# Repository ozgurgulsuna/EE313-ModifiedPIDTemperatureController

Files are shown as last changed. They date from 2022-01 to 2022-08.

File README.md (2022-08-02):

<h3 align="center" style=" border-bottom: none ;">EE313 Term Project </h3>
<p align="center">
   
<h2 align="center" style=" border-bottom: none ;">Design of an Autonomous Temperature Conditioning System Using Modified Analog PID Controller</h2>
<p align="center">

<h3 align="center" style=" border-bottom: none ;"> Project Summary </h3>
<p align="center">

<p align="justify">
&nbsp&nbsp Air conditioning can be described as the process of cooling, heating, moisturizing, dehumidifying, etc.
This method is utilized to create a more pleasant interior environment. In this project, you are required
to design an air conditioner system for small spaces. The system acquires heating, and cooling functions
and consists of one variable set input and four subsystems, namely, the control unit, display unit, sensing
unit, and the operation unit. The sensing unit provides the ambient temperature to the control unit, and
the temperature adjustment unit provides the desired temperature to the control unit. Figure 1 shows
the block diagram of the system.
</p>

<p align="center">
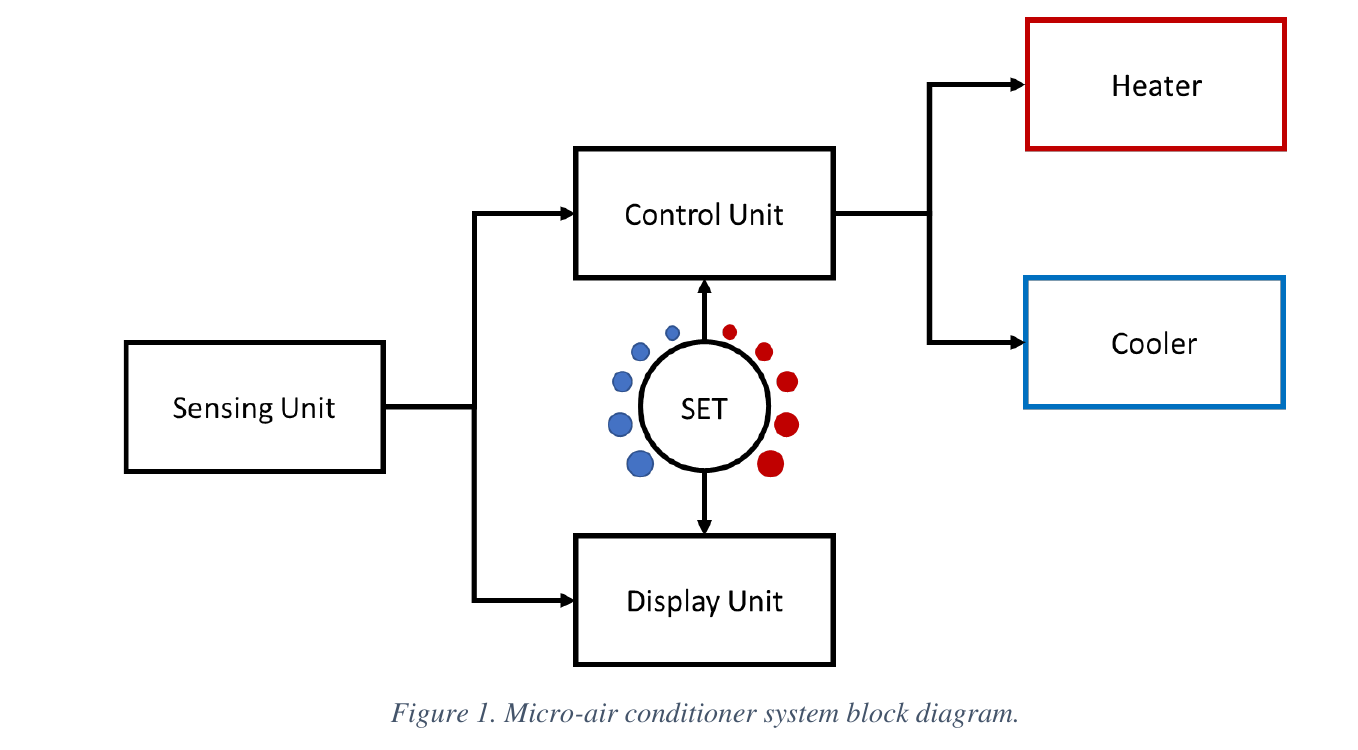
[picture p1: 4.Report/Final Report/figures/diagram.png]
 </a>
</p>

<p align="justify">
&nbsp&nbsp Thus to design a responsive, fast, and accurate temperature control system PID method is a feasible choice. One challenge, of applying PID method to this problem is that the heating and cooling processes are not symmetric. To compensate that, a modified PID control circuit will be introduced in this paper. Also, to avoid the EMI (Electromagnetic Interference) and noise problems, the circuit is designed on a PCB (Printed Circuit Board). The heating element is a nickel-chromium wire and the cooling element is an 12V DC fan. The fan and the heater are driven with a MOSFET switch which is controlled by the generated PWM (Pulse Width Modulation) signals. The PWM for each switch is generated by comparing a triangular wave with the PID outputs.
</p>
   
<p align="justify">
&nbsp&nbsp The ambient temperature is measured using the LM35 analog temperature sensor. The set temperature value is adjusted with a potentiometer. The set and ambient temperatures are displayed by the display unit which consist of RGB LEDs (Red Green Blue Light Emitting Diodes), a constant current LED drive utilized by a transconductance amplifier. The display unit designed in a way to emit red light at 24°Cand below, green light at 32°Cand blue light at 40°C and above. The display output for the temperature intervals between those values are produced by combining the colors in a way that a smooth transition is observed while the set and ambient temperatures are changed.
</p>

<p align="justify">
&nbsp&nbsp In this project, first the design methodology and the mathematical analysis of each unit will be discussed in detail in section II. The circuit schematics and their analysis will be given in this part. The mechanical design and the manufacturing will be discussed in section III. Then, thermal modelling of the system will be explained in section IV. The results of the performed LTspice simulations will be given in section V. The experimental results and the comparison with the simulation will follow in section VI. Finally, the conclusions will be drawn in section VII.
</p>

<h3 align="center" style=" border-bottom: none ;"> Report </h3>
<p align="center">
   
<p align="justify">
&nbsp&nbsp In this <a href="https://github.com/ozgurgulsuna/EE313-ModifiedPIDTemperatureController/blob/main/Design%20of%20an%20Autonomous%20Temperature%20Conditioning%20System%20Using%20Modifi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">report </a>, the design and implementation of an autonomous temperature conditioning system is demonstrated. Electrical and thermal systems are modelled in a single simulation environment with feedback loop closed. The PID method is shown that its applicable to this system, but due to the asymmetry of the reverse processes a modified PID circuit is proposed to damp oscillations of the system around the steady state, which is shown to be successful with the experimental results. Moreover, since the control signals are critical for the process, it is observed that filtering the noise with low and high pass filters and also avoiding the EMI effects with a careful PCB design procedure is essential for an accurate and reliable control mechanism.
</p>

<p align="center">
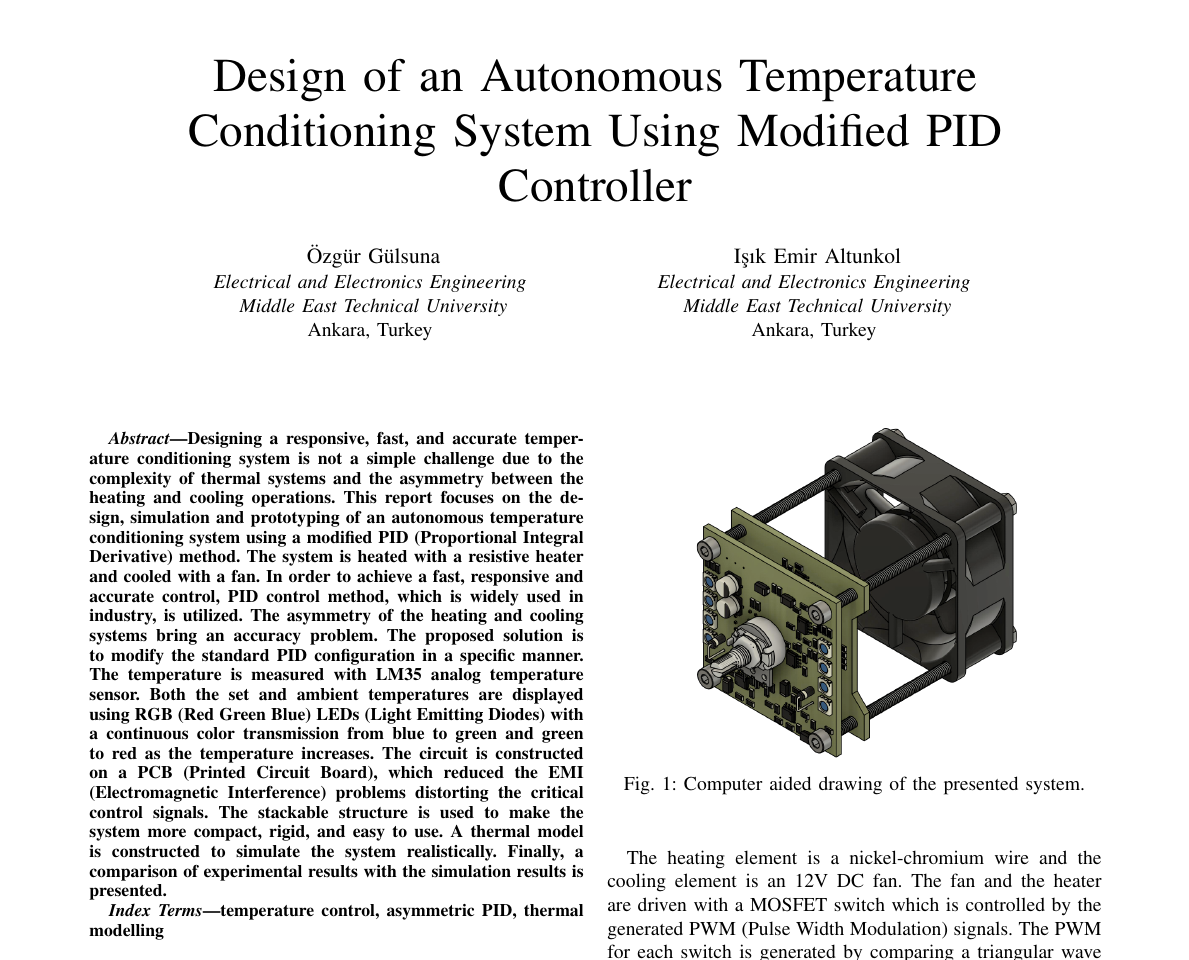
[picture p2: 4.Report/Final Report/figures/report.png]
   </a>
</p>

<h3 align="center" style=" border-bottom: none ;"> Photographs </h3>

<p align="center">
   
<p align="center">
    
    &nbsp&nbsp 
    
</p>

<p align="center">
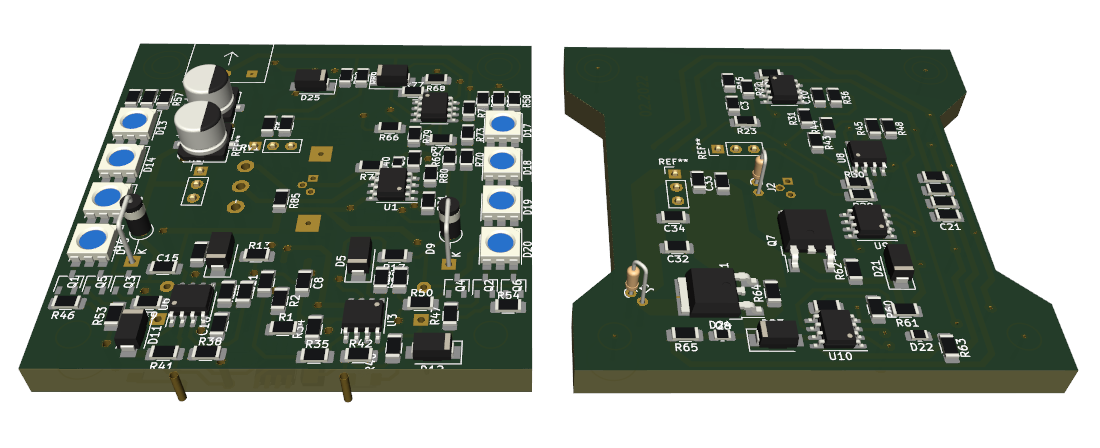
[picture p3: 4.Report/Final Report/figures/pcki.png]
    
</p>

<p align="center">
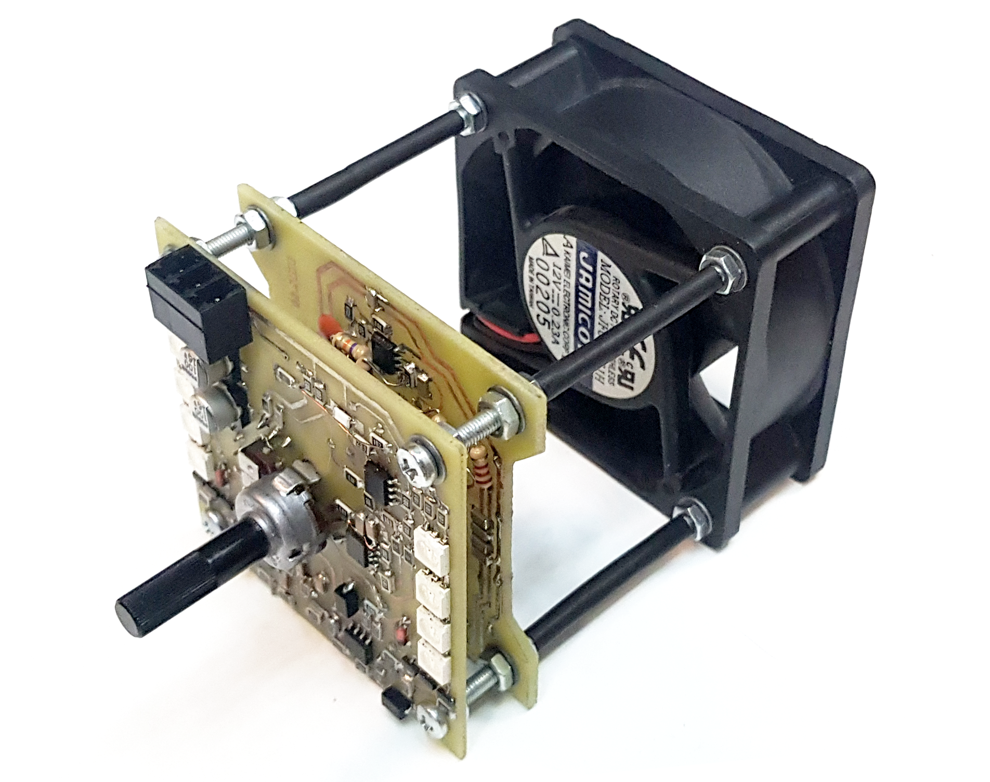
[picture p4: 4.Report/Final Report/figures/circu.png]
    
    &nbsp&nbsp 
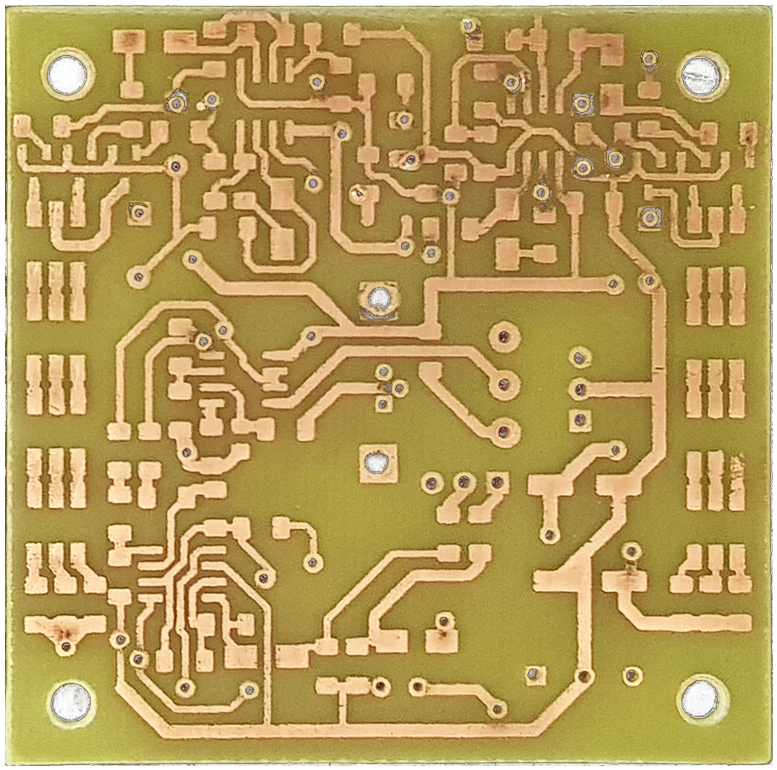
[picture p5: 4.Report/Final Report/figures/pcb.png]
    
</p>

<p align="center">
    
</p>
<p align="center">
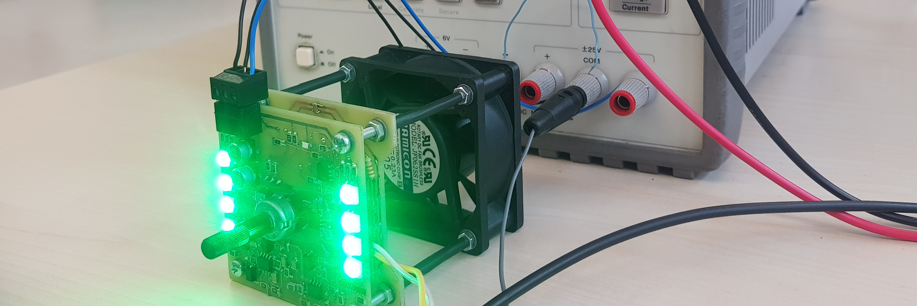
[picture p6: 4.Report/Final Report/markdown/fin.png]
    
</p>

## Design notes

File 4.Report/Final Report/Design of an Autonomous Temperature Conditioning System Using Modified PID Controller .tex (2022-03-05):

\documentclass[conference]{IEEEtran}
\IEEEoverridecommandlockouts
% The preceding line is only needed to identify funding in the first footnote. If that is unneeded, please comment it out.
\usepackage{cite}
\usepackage{amsmath,amssymb,amsfonts}
\usepackage{algorithmic}
\usepackage{graphicx}
\usepackage{textcomp}
\usepackage{xcolor}

\usepackage{physics}
\usepackage{amsmath}
\usepackage{tikz}
\usepackage{mathdots}
\usepackage{yhmath}
\usepackage{cancel}
\usepackage{color}
\usepackage{siunitx}
\usepackage{array}
\usepackage{multirow}
\usepackage{amssymb}
\usepackage{gensymb}
\usepackage{tabularx}
\usepackage{extarrows}
\usepackage{booktabs}
\usetikzlibrary{fadings}
\usetikzlibrary{patterns}
\usetikzlibrary{shadows.blur}
\usetikzlibrary{shapes}
\usepackage[figure]{ragged2e}

\usepackage{graphicx}
\usepackage{caption}
\usepackage{subcaption}

\def\BibTeX{{\rm B\kern-.05em{\sc i\kern-.025em b}\kern-.08em
    T\kern-.1667em\lower.7ex\hbox{E}\kern-.125emX}}
\begin{document}

\title{Design of an Autonomous Temperature Conditioning System Using Modified PID Controller\\
{}
}

\author{\IEEEauthorblockN{Özgür Gülsuna}
\IEEEauthorblockA{\textit{Electrical and Electronics Engineering} \\
\textit{Middle East Technical University}\\
Ankara, Turkey \\}
\and
\IEEEauthorblockN{Işık Emir Altunkol}
\IEEEauthorblockA{\textit{Electrical and Electronics Engineering} \\
\textit{Middle East Technical University}\\
Ankara, Turkey \\}
}

\maketitle

\begin{abstract}
Designing a responsive, fast, and accurate temperature conditioning system is not a simple challenge due to the complexity of thermal systems and the asymmetry between the heating and cooling operations. This report focuses on the design, simulation and prototyping of an autonomous temperature conditioning system using a modified PID (Proportional Integral Derivative) method. The system is heated with a resistive heater and cooled with a fan. In order to achieve a fast, responsive and accurate control, PID control method, which is widely used in industry, is utilized. The asymmetry of the heating and cooling systems bring an accuracy problem. The proposed solution is to modify the standard PID configuration in a specific manner. The temperature is measured with LM35 analog temperature sensor. Both the set and ambient temperatures are displayed using RGB (Red Green Blue) LEDs (Light Emitting Diodes) with a continuous color transmission from blue to green and green to red as the temperature increases. The circuit is constructed on a PCB (Printed Circuit Board), which reduced the EMI (Electromagnetic Interference) problems distorting the critical control signals. The stackable structure is used to make the system more compact, rigid, and easy to use. A thermal model is constructed to simulate the system realistically. Finally, a comparison of experimental results with the simulation results is presented.
\end{abstract}

\begin{IEEEkeywords}
temperature control, asymmetric PID, thermal modelling
\end{IEEEkeywords}

\section{Introduction}
In the industry, various control techniques are used for automating the physical processes. One of the simplest one is the on-off control, in which the operating unit is either actuated or not depending on other system and state parameters. However, the on-off control method is not flexible and accurate for most of the control problems. Because of that a slightly more advanced method called PID (Proportional Integral Derivative) is widely utilized in industry.

\begin{figure}[ht]
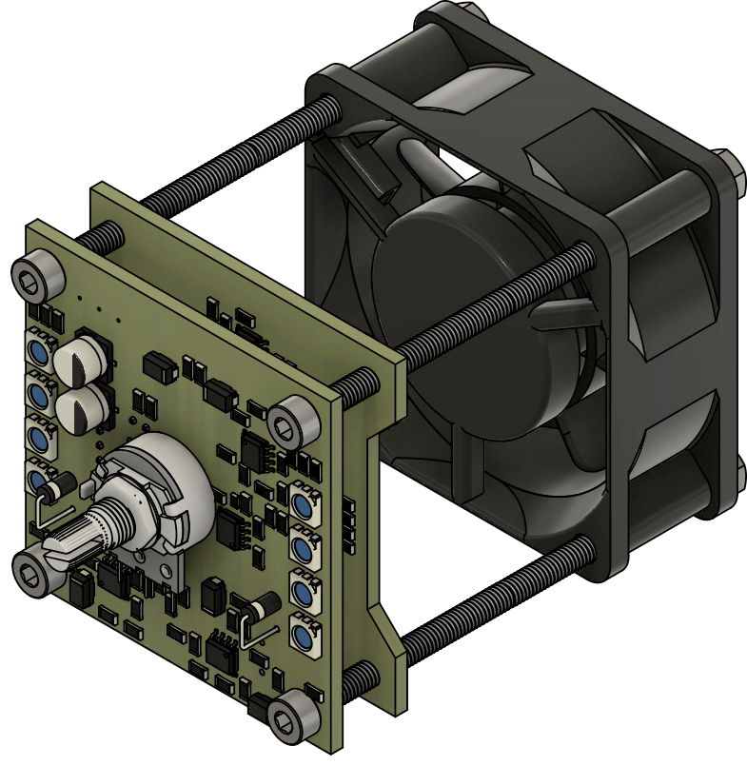
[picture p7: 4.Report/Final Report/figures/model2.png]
\centerline{}
\caption{Computer aided drawing of the presented system.}
\label{}
\end{figure}

Thus to design a responsive, fast, and accurate temperature control system PID method is a feasible choice. One challenge of applying PID method to this problem is that the heating and cooling processes are not symmetric. To compensate that, a modified PID control circuit will be introduced in this paper. Also, to avoid the EMI (Electromagnetic Interference) and noise problems, the circuit is designed on a PCB (Printed Circuit Board).

The heating element is a nickel-chromium wire and the cooling element is an 12V DC fan. The fan and the heater are driven with a MOSFET switch which is controlled by the generated PWM (Pulse Width Modulation) signals. The PWM for each switch is generated by comparing a triangular wave with the PID outputs.

The ambient temperature is measured using the LM35 analog temperature sensor. The set temperature value is adjusted with a potentiometer. The set and ambient temperatures are displayed by the display unit which consist of RGB LEDs (Red Green Blue Light Emitting Diodes), a constant current LED drive utilized by a transconductance amplifier. The display unit designed in a way to emit red light at 24\celsius and below, green light at 32\celsius and blue light at 40\celsius and above. The display output for the temperature intervals between those values are produced by combining the colors in a way that a smooth transition is observed while the set and ambient temperatures are changed.

In this paper, first the design methodology and the mathematical analysis of each unit will be discussed in detail in section II. The circuit schematics and their analysis will be given in this part. The mechanical design and the manufacturing will be discussed in section III. Then, thermal modelling of the system will be explained in section IV. The results of the performed LTspice simulations will be given in section V. The experimental results and the comparison with the simulation will follow in section VI. Finally, the conclusions will be drawn in section VII.

\section{Design Methodology and Mathematical Analysis}

In this section the design criteria are analyzed and solutions to each unit is presented with mathematical analysis of circuits are explained in detail.
 
\subsection{Sensing Unit}

The sensing unit consists of two independent sub-sections as mentioned above. The first element is the LM35 temperature sensor. This sensor gives a linear analog voltage output between -55$ ^\circ$C and 150  $ ^\circ$C in consequence it is applicable for the designs needs. The output of this sensor is amplified to ten folds such that 28$^\circ$C is scaled as 2.8 volts. This primary amplification facilitates the signal in order to better process it in the later stages. The second element is a potentiometer, which is basically a reference input and it is used in an adjustable resistor division configuration which scales the position to the range between 2 volts and 4.5 volts to cover the operation range of 20 to 45 $^\circ$C.

As in most of the sensory data acquisition, an initial low pass filter is used to clear out the unwanted high-frequency signals\cite{b1}. The design for this initial unit has an R-C low pass filter with the cut off frequency of 338.6 Hz \eqref{filter} which is selected as it is around 1/3 of the switching frequency of the operation unit. 
\begin{equation*}
f_{cut-off} =\frac{1}{2\pi RC} \rightarrow 338.6\ Hz \label{filter}
\end{equation*}

Another feature this section has is a linear regulator to supply the LM35 sensor. The selected voltage regulator is LM7805 which is a linear type and it is used to isolate the input of the temperature sensor from the unwanted swing of the input voltage.

\begin{figure}[h]
\centerline{}
\caption{Circuit schematic of the sensing unit}
\label{fig}
\end{figure}

The outputs of this unit are forwarded to the display and control units.

\subsection{Display Unit}

The display unit takes two inputs from the sensing unit: one is the amplified ambient temperature signal and the other is the set value, which is scaled to the same range with the temperature signal. This unit produces three different voltage signals to drive the RGB LEDs (one for each color), both for the set value display and the ambient temperature display. Since LED brightness is linearly proportional with its current, a transconductance amplifier with a BJT (Bipolar Junction Transistor) is used as a constant current LED driver (Fig.~\ref{transcondAmp}). Assuming the BJT is in forward active operation:

\begin{figure}[h]
\centerline{}
\caption{Transconductance amplifier as a constant current driver}
\label{transcondAmp}
\end{figure}

\begin{equation}
I_{C} = \beta \times \frac{V_{in}-V_{BE_{on}}}{R_{B}}\label{Iled}
\end{equation}

By \eqref{Iled}, it is observed that the input voltage signal is shifted downwards by $V_{BE_{on}}$ and then amplified by $\frac{\beta}{R_{B}}$. The collector current needed for the corresponding amplifier to obtain the required brightness for each color terminal is given in Fig.~\ref{ILED}.

\begin{figure}[h]
\centerline{}
\vspace{-1em}
\caption{Current vs temperature for each color terminal}
\label{ILED}
\end{figure}

To obtain the current signal in Fig.~\ref{ILED}, the voltage $V_{in}$ must be in the same shape, but shifted up by $V_{BE_{on}}$. This is why there is an amplifier stage which adds the diode drop value to the amplified set and temperature voltages. The schematic of these amplifiers is given in figure Fig.~\ref{dropSubtracter}. It can be easily observed that the input output relation for the amplifiers in figure Fig.~\ref{dropSubtracter} is given as:

\begin{equation}
V_{1}' = 2\cdot V_{1}+V_{BE_{on}}\label{drop_sub}
\end{equation}

\begin{figure}[h]
\centerline{}
\caption{Circuit schematic for $V_{BE_{on}}$ compensator}
\label{dropSubtracter}
\end{figure}

Note that the diode drop and the base emitter voltage drop of the transistors are approximately equal, since they are both made of silicon. The zener diode connected in shunt clips the voltage above 6.8V, which creates an upper limit for input voltage of the transconductance amplifier. Considering these, the process for obtaining the red and blue LED currents is the following: An offset is added to the temperature signal (or the set value signal, for the set display) to align its 0 value to the center of the operation region of the circuit (32\celsius). Then, this new signal is connected to $V_{1}$ \& $V_{2}$ terminals of the amplifier in figure Fig.~\ref{dropSubtracter}. Finally, determining $R_{C}=120k\Omega$ and connecting the output of the compensator to the input of the transconductance amplifier, we obtain the desired current signal.

A straightforward way to obtain the green LED current is to use an inverting summing amplifier and sum the voltage signals produced at the outputs of the figure Fig.~\ref{dropSubtracter}, and transmit this sum to the input of the transconductance amplifier. Note that the inverting sum result is a shifted version of the desired voltage, therefore the appropriate offset should be applied during the summing operation. Connecting all of the aforementioned parts, a display unit with a smooth and precise output is designed.

\subsection{Control Unit}
One of the more ingenious ways of controlling a dynamic system is PID method. This three-term controller is commonly used in the industry because of its accuracy and responsiveness \cite{b2}. Therefore it is selected as the main controller, more precisely a version with parallel configuration of action parameters of PID is selected. This approach isolates the parameters from each other which provides an easier tuning procedure for our system.

The system has two process variables in other words two outputs that can be controlled with our controller. These two actuators, heating element and fan, are working asynchronous with opposite reactions. This duality enforces an asymmetry in our system and it should be addressed to improve the response of the system \cite{b3}. The first solution comes in mind is to separate the controllers for each process variable but it increases the cost both in terms of components and tuning time. Our proposed method utilizes a single PID controller for the heater and its output is passed through a proportional term which then it is fed to the fan. This cascaded configuration presented in Fig.~\ref{parallelPID} enables the system to utilize its integral and derivative terms in both of the outputs. 

\begin{figure}[h]

\tikzset{every picture/.style={line width=0.75pt}} %set default line width to 0.75pt        

\begin{tikzpicture}[x=0.47pt,y=0.47pt,yscale=-1,xscale=1]
%uncomment if require: \path (0,235); %set diagram left start at 0, and has height of 235

%Shape: Resistor [id:dp04371691643945974] 
\draw   (135.96,39) -- (246.04,39) -- (246.04,79) -- (135.96,79) -- (135.96,39) -- cycle (105,59) -- (135.96,59) (246.04,59) -- (277,59) ;
%Shape: Resistor [id:dp10680848125616538] 
\draw   (135.96,94) -- (246.04,94) -- (246.04,134) -- (135.96,134) -- (135.96,94) -- cycle (105,114) -- (135.96,114) (246.04,114) -- (277,114) ;
%Shape: Resistor [id:dp6702844773190892] 
\draw   (135.96,150) -- (246.04,150) -- (246.04,190) -- (135.96,190) -- (135.96,150) -- cycle (105,170) -- (135.96,170) (246.04,170) -- (277,170) ;
%Straight Lines [id:da9493111687595024] 
\draw    (105,59) -- (105,170) ;
%Straight Lines [id:da22129182527616287] 
\draw    (105,59) -- (133.96,59) ;
\draw [shift={(135.96,59)}, rotate = 180] [color={rgb, 255:red, 0; green, 0; blue, 0 }  ][line width=0.75]    (10.93,-3.29) .. controls (6.95,-1.4) and (3.31,-0.3) .. (0,0) .. controls (3.31,0.3) and (6.95,1.4) .. (10.93,3.29)   ;
%Straight Lines [id:da46981664928370725] 
\draw    (105,114) -- (133.96,114) ;
\draw [shift={(135.96,114)}, rotate = 180] [color={rgb, 255:red, 0; green, 0; blue, 0 }  ][line width=0.75]    (10.93,-3.29) .. controls (6.95,-1.4) and (3.31,-0.3) .. (0,0) .. controls (3.31,0.3) and (6.95,1.4) .. (10.93,3.29)   ;
%Straight Lines [id:da05179885664599704] 
\draw    (105,170) -- (133.96,170) ;
\draw [shift={(135.96,170)}, rotate = 180] [color={rgb, 255:red, 0; green, 0; blue, 0 }  ][line width=0.75]    (10.93,-3.29) .. controls (6.95,-1.4) and (3.31,-0.3) .. (0,0) .. controls (3.31,0.3) and (6.95,1.4) .. (10.93,3.29)   ;
%Straight Lines [id:da6012096316257116] 
\draw    (246.04,114) -- (275,114) ;
\draw [shift={(277,114)}, rotate = 180] [color={rgb, 255:red, 0; green, 0; blue, 0 }  ][line width=0.75]    (10.93,-3.29) .. controls (6.95,-1.4) and (3.31,-0.3) .. (0,0) .. controls (3.31,0.3) and (6.95,1.4) .. (10.93,3.29)   ;
%Straight Lines [id:da20403881397537615] 
\draw    (288.5,170) -- (288.5,127.5) ;
\draw [shift={(288.5,125.5)}, rotate = 90] [color={rgb, 255:red, 0; green, 0; blue, 0 }  ][line width=0.75]    (10.93,-3.29) .. controls (6.95,-1.4) and (3.31,-0.3) .. (0,0) .. controls (3.31,0.3) and (6.95,1.4) .. (10.93,3.29)   ;
%Straight Lines [id:da27228914592677467] 
\draw    (288.5,59) -- (288.5,100.5) ;
\draw [shift={(288.5,102.5)}, rotate = 270] [color={rgb, 255:red, 0; green, 0; blue, 0 }  ][line width=0.75]    (10.93,-3.29) .. controls (6.95,-1.4) and (3.31,-0.3) .. (0,0) .. controls (3.31,0.3) and (6.95,1.4) .. (10.93,3.29)   ;
%Flowchart: Summing Junction [id:dp5290671545073427] 
\draw   (277,114) .. controls (277,107.65) and (282.15,102.5) .. (288.5,102.5) .. controls (294.85,102.5) and (300,107.65) .. (300,114) .. controls (300,120.35) and (294.85,125.5) .. (288.5,125.5) .. controls (282.15,125.5) and (277,120.35) .. (277,114) -- cycle ; \draw   (280.37,105.87) -- (296.63,122.13) ; \draw   (296.63,105.87) -- (280.37,122.13) ;
%Straight Lines [id:da746161281015258] 
\draw    (277,170) -- (288.5,170) ;
%Straight Lines [id:da11789860127120222] 
\draw    (277,59) -- (288.5,59) ;
%Straight Lines [id:da810785702729852] 
\draw    (78,114) -- (105,114) ;
%Straight Lines [id:da03181312676625048] 
\draw    (300,114) -- (510,114) ;
%Shape: Resistor [id:dp25780959233444034] 
\draw   (375.96,150) -- (486.04,150) -- (486.04,190) -- (375.96,190) -- (375.96,150) -- cycle (345,170) -- (375.96,170) (486.04,170) -- (517,170) ;
%Straight Lines [id:da21977667644036813] 
\draw    (345,170) -- (373.96,170) ;
\draw [shift={(375.96,170)}, rotate = 180] [color={rgb, 255:red, 0; green, 0; blue, 0 }  ][line width=0.75]    (10.93,-3.29) .. controls (6.95,-1.4) and (3.31,-0.3) .. (0,0) .. controls (3.31,0.3) and (6.95,1.4) .. (10.93,3.29)   ;
%Straight Lines [id:da016506681158132253] 
\draw    (345,170) -- (345,113.67) ;
%Straight Lines [id:da8718572314475974] 
\draw    (486.04,170) -- (515,170) ;
\draw [shift={(517,170)}, rotate = 180] [color={rgb, 255:red, 0; green, 0; blue, 0 }  ][line width=0.75]    (10.93,-3.29) .. controls (6.95,-1.4) and (3.31,-0.3) .. (0,0) .. controls (3.31,0.3) and (6.95,1.4) .. (10.93,3.29)   ;
%Straight Lines [id:da33938783257620053] 
\draw    (300,114) -- (515,114) ;
\draw [shift={(517,114)}, rotate = 180] [color={rgb, 255:red, 0; green, 0; blue, 0 }  ][line width=0.75]    (10.93,-3.29) .. controls (6.95,-1.4) and (3.31,-0.3) .. (0,0) .. controls (3.31,0.3) and (6.95,1.4) .. (10.93,3.29)   ;

% Text Node
\draw (177,49.4) node [anchor=north west][inner sep=0.75pt]  [font=\small]   {$K_{p} e( t)$};
% Text Node
\draw (168,103.4) node [anchor=north west][inner sep=0.75pt]  [font=\small]     {${\textstyle K_{i}\int e( t)}$};
% Text Node
\draw (173,159.4) node [anchor=north west][inner sep=0.75pt]   [font=\small]    {${\textstyle K_{d}\frac{d\ e( t)}{dt}}$};
% Text Node
\draw (68,91.4) node [anchor=north west][inner sep=0.75pt]   [font=\small]    {$e( t)$};
% Text Node
\draw (519.49,95.4) node [anchor=north west][inner sep=0.75pt]   [font=\small]    {$u_{heater}( t)$};
% Text Node
\draw (424.82,161.73) node [anchor=north west][inner sep=0.75pt]   [font=\small]    {$K_{p} e( t)$};
% Text Node
\draw (142,53.4) node [anchor=north west][inner sep=0.75pt]  [font=\large]  {${\displaystyle \mathbf{P}_{\mathbf{1}}}$};
% Text Node
\draw (142,103.4) node [anchor=north west][inner sep=0.75pt]  [font=\large]  {$\mathbf{I}$};
% Text Node
\draw (142,161.4) node [anchor=north west][inner sep=0.75pt]  [font=\large]  {$\mathbf{D}$};
% Text Node
\draw (382,161.4) node [anchor=north west][inner sep=0.75pt]  [font=\large]  {${\displaystyle \mathbf{P}_{\mathbf{2}}}$};
% Text Node
\draw (524.16,152.73) node [anchor=north west][inner sep=0.75pt]    {$u_{fan}( t)$};

\end{tikzpicture}

\caption{Proposed modified PID controller block diagram.}
\label{parallelPID}
\end{figure}

The controller in this section is implemented using operational amplifiers in an analogous way. First the error is generated using non inverting difference amplifier with unity gain. The error is then passed to three parallel stages which are proportional, integral and derivative terms. These configurations are inverting amplifiers by nature. Then the inverting summing amplifier is used to sum the action parameters into one. The circuit diagram of the control unit can be seen in Fig.~\ref{PIDcct}.

\begin{figure}[h]
    \centering
    
    \caption{PID implementation using operational amplifiers}
    \label{PIDcct}
\end{figure}

Key point of the control unit is the derivative term. Differentiator amplifier circuit acts as a high pass filter, in other words it enables high frequency components of the input signal to not only to pass but to be amplified \cite{b4}. It is an undesired condition since our switching frequency is around 1 kHz and it is easily coupled into the error signal. Amplifying this noise signal can cause the control signal to become erratic. Analyzing the differentiator circuit given in Fig.~\ref{diffe} shows this phenomena more clearly.

\begin{figure}[h]
    \centering
    
    \caption{Differentiator circuit to be analyzed.}
    \label{diffe}
\end{figure}

As seen in \eqref{derform} for high frequencies impedance of the capacitor is very small and in absence of $R_C$ resistor the gain is very high. In order to limit this gain a resistor of 1 k$\Omega$ is selected. 

\begin{equation}
V_{out} =\frac{-V_{error}R_D}{R_C + \frac{1}{sC_D}}\label{derform}
\end{equation}

\subsection{Operation Unit}

The purpose of the operation unit is to take the PID output signals from the control unit and produce PWM signals to drive the heater and the fan using a switch. The PWM method is utilized to convert the analog signals of the control unit into digital signals that can drive the MOSFETs. 

The first stage is a triangular wave generator (Fig.~\ref{triGen}). The left part in Fig.~\ref{triGen} is an astable multivibrator, which creates a square wave with the frequency given as:

\begin{equation}
f=\frac{1}{2R_{1}C_{1}\ln{(1+\frac{2R_{3}}{R_{2}})}}\label{freq}
\end{equation}

\begin{figure}[h]
\centerline{}
\caption{Circuit schematic of the triangular wave generator}
\label{triGen}
\end{figure}

Since it is aimed to achieve a PWM frequency around $1kHz$, the component values are chosen as $R_{1}=4.7k\Omega, C_{1}=22nF, R_{2}=1k\Omega, R_{3}=47k\Omega$ which brings $1.062kHz$ by \eqref{freq}. The multivibrator output is given to the integrator circuit, whose time constant is chosen as $R_{4}C_{2}=5ms$. Thus, $0.2$ time constant of the exponential waveform is produced, which is close enough to a triangular wave. After adding an offset and amplifying to an appropriate range, the triangular wave is supplied to two comparators to generate the PWM signals. The minimum points of the final triangular wave is higher than 0 volts by a couple hundred mVs, so that the heather or the fan does not act even for small disturbances in the control signals.

The PWM generating process for the heater is done in the conventional way. The triangular wave is compared with the PID heater output signal, and then a MOSFET is used as a switch to drive the heater with the PWM signal. The same process is applied to for the fan, except that after the cooperator, an additional compactor step is added to avoid powering the fan while the heater operates (Fig.~\ref{fanAND}). The second op-amp stage checks if the PID heater output is still higher than a certain threshold voltage (which is a positive value close to 0), and turns the switch on only if it is smaller than the threshold voltage. In this way, our design criteria is satisfied.

\begin{figure}[h]
\centerline{}
\caption{Circuit schematic of the comparators}
\label{fanAND}
\end{figure}

While the heater operates, the maximum power consumed by the system is less than 12W.

\section{Mechanical Design and Manufacturing}
Design of the mechanical system is formed around the biggest component which is the fan. It is 60x60 mm in width and 25 mm in depth with four bolt holes on four corners. These holes are used with 3mm bolts to construct a frame around the fan and circuit elements. These elements consist of operational amplifiers, LEDs, passive components such as resistors and capacitors and heater with the temperature sensor. All elements are fixed on printed circuit board (PCB) besides the fan. To satisfy the small form factor criteria PCB dimensions are selected again 60x60 mm and surface mount components are used. 

Heater element is a nickel-chromium wire which is used in electric heaters.The wire is wrapped into a spring shape and formed into a circle around the temperature sensor.This element has advantages such as enduring high temperatures, having a relatively high resistance which makes it smaller and being malleable. 

The power connector has three pins 12V, ground and -12V respectively. It connects only one way which makes it more convenient.

PCB is designed to form the circuit on. This technology has two advantages on analog circuits. The first one is with careful track planning noise susceptibility is reduced. The parasitic resistances, inductances and capacitances are also minimized. The second advantage is its rigidity and compactness. Design of the PCB is done on KiCad which is an open-source circuit board drawing program. The design consist two double-sided boards with connectors in-between. This stackable composition has advantages in both initial testing of the boards and in isolating the power paths from signal paths. The more outer board consist of sensing unit, display unit and control unit. All of these units consume very little power and they produce the control signals. The second board only has the operation unit. The most of the power is directed through this board. The PWM method creates changing currents and when we look at the equation of induced voltage in \eqref{indVolt}. It can be observed that time altering magnetic field generated from AC currents of the PWM signals, induces emf voltage on the magnetically coupled regions of the circuit. This way the noise is transmitted on signal paths. 

\begin{equation}
V_{ind} = L\frac{di}{dt} \label{indVolt}    
\end{equation}

Separating the boards reduces this interference and effectively isolates the signal paths. 

Input bus capacitors and decoupling capacitors near the operational amplifiers are working in a similar manner. These components filter out the noise from the input source and reduce the conducted EMI (Electromagnetic Interference) between sections.

\begin{figure}[!tbp]
  \begin{subfigure}[b]{0.319\textwidth}
    
    \caption{print out of the design.}
    \label{PCB}
  \end{subfigure}
  \hfill
  \begin{subfigure}[b]{0.158\textwidth}
    
    \caption{Printed circuit.}
    \label{}
  \end{subfigure}
  \begin{subfigure}{0.5\textwidth}
    
    \caption{3D model of the circuit board.}
  \end{subfigure}
  \caption{Digital and manufactured outputs of the PCB.}
\end{figure}

Manufacturing of this PCB is done with copper etching process using basic tools such as laser toner printer, clothes iron and corrosive chemicals. The printouts of the PCB for both boards and layers with processed PCB can be seen in Fig.\ref{PCB}.

\begin{figure}
\centerline{}
\caption{Hardware prototype of the designed temperature conditioning system.}
\end{figure}

\section{Thermal Modeling}
This project is composed of two mediums, electrical and thermal. The thermal system consist of heater, fan, temperature sensor and materials in-between. The electrical circuit is as mentioned, consist of the required circuitry to convert the electrical energy to thermal energy. 

In order to simulate the system as a whole it is needed to model the thermal system in electrical analogy. In this analogy, voltage corresponds to the temperature, current corresponds to the heat transfer ratio i.e. power and resistance  corresponds to the thermal resistance. Considering the elements of the thermal system the network is modeled as in Fig. \ref{Thermal}. $R_{\Theta HA}$ is the thermal resistance between the heater and ambient, $R_{\Theta HS}$ is between heater and sensor and $R_{\Theta SA}$ is between sensor and the ambient. The heater is a power controlled current source and the ambient is a fixed voltage source at the room temperature. Lastly the thermal capacitance of the temperature senor is given $C_{sens}$ and nickel-chromium wire is assumed to have very low thermal capacitance while it is very high for the ambient air.

From the datasheet of the LM35 temperature sensor we can find that $R_{\Theta SA}$ is 180 $^\circ C/W$ for the still air. To find the thermal resistance between the heater and the temperature sensor a test is conducted where a known power is applied to the heater and from the temperature difference between the ambient and the sensor with known $R_{\Theta SA}$ the heat flow ratio through the sensor to the ambient is calculated, that is:

\begin{equation}
    \frac{V_{sense}-V_{ambient}}{R_{\Theta SA}}=I_{branch1}
\end{equation}

\begin{equation}
    \frac{V_{heater}-V_{sens}}{I_{branch1}}=R_{\Theta HS}
\end{equation}

\begin{figure}[h]

\centering

\tikzset{every picture/.style={line width=0.75pt}} %set default line width to 0.75pt        

\begin{tikzpicture}[x=0.65pt,y=0.65pt,yscale=-1,xscale=1]
%uncomment if require: \path (0,241); %set diagram left start at 0, and has height of 241

%Shape: Resistor [id:dp19155962871671584] 
\draw   (263,120.55) -- (274.27,120.55) -- (276.77,113) -- (281.78,128.1) -- (286.79,113) -- (291.8,128.1) -- (296.8,113) -- (301.81,128.1) -- (306.82,113) -- (311.83,128.1) -- (314.33,120.55) -- (325.6,120.55) ;
%Shape: Capacitor [id:dp5418351324101072] 
\draw   (351.2,120.55) -- (351.2,152.61) (367.35,159.74) -- (335.05,159.74) (367.35,152.61) -- (335.05,152.61) (351.2,159.74) -- (351.2,191.8) ;
%Straight Lines [id:da2477799830980456] 
\draw    (325.6,120.55) -- (351.2,120.55) ;
%Straight Lines [id:da628273924807907] 
\draw    (351.2,120.55) -- (376.8,120.55) ;
%Shape: Resistor [id:dp5586121261918382] 
\draw   (376.8,120.55) -- (388.07,120.55) -- (390.57,113) -- (395.58,128.1) -- (400.59,113) -- (405.6,128.1) -- (410.6,113) -- (415.61,128.1) -- (420.62,113) -- (425.63,128.1) -- (428.13,120.55) -- (439.4,120.55) ;
%Straight Lines [id:da07949068449386076] 
\draw    (237.4,120.55) -- (263,120.55) ;
%Straight Lines [id:da6123881332149554] 
\draw    (439.4,120.55) -- (465,120.55) ;
%Flowchart: Connector [id:dp3224089439007152] 
\draw   (449.15,156.25) .. controls (449.15,147.5) and (456.25,140.4) .. (465,140.4) .. controls (473.75,140.4) and (480.85,147.5) .. (480.85,156.25) .. controls (480.85,165) and (473.75,172.1) .. (465,172.1) .. controls (456.25,172.1) and (449.15,165) .. (449.15,156.25) -- cycle ;
%Straight Lines [id:da8184153667034564] 
\draw    (465,120.55) -- (465,140.4) ;
%Straight Lines [id:da051595058920608006] 
\draw    (465,172.1) -- (465,191.95) ;
%Straight Lines [id:da6642435742487613] 
\draw    (237.4,120.55) -- (237.4,140.4) ;
%Straight Lines [id:da8967564739142377] 
\draw    (237.4,172.1) -- (237.4,191.95) ;
%Flowchart: Connector [id:dp07363181952530651] 
\draw   (221.55,156.25) .. controls (221.55,147.5) and (228.65,140.4) .. (237.4,140.4) .. controls (246.15,140.4) and (253.25,147.5) .. (253.25,156.25) .. controls (253.25,165) and (246.15,172.1) .. (237.4,172.1) .. controls (228.65,172.1) and (221.55,165) .. (221.55,156.25) -- cycle ;
%Shape: Ground [id:dp6306543326034124] 
\draw   (228.58,197.97) -- (237.4,210) -- (246.23,197.97) -- (228.58,197.97) -- cycle (237.4,191.95) -- (237.4,197.97) ;
%Shape: Ground [id:dp3092481158515603] 
\draw   (342.38,197.82) -- (351.2,209.85) -- (360.03,197.82) -- (342.38,197.82) -- cycle (351.2,191.8) -- (351.2,197.82) ;
%Shape: Ground [id:dp36715519214038794] 
\draw   (456.18,197.97) -- (465,210) -- (473.83,197.97) -- (456.18,197.97) -- cycle (465,191.95) -- (465,197.97) ;
%Straight Lines [id:da5206072269602895] 
\draw    (237.4,164) -- (237.4,148.4) ;
\draw [shift={(237.4,146.4)}, rotate = 90] [color={rgb, 255:red, 0; green, 0; blue, 0 }  ][line width=0.75]    (7.65,-2.3) .. controls (4.86,-0.97) and (2.31,-0.21) .. (0,0) .. controls (2.31,0.21) and (4.86,0.98) .. (7.65,2.3)   ;
%Shape: Resistor [id:dp2796434337397189] 
\draw   (319.2,77.35) -- (330.47,77.35) -- (332.97,69.8) -- (337.98,84.9) -- (342.99,69.8) -- (348,84.9) -- (353,69.8) -- (358.01,84.9) -- (363.02,69.8) -- (368.03,84.9) -- (370.53,77.35) -- (381.8,77.35) ;
%Straight Lines [id:da12366662536381101] 
\draw    (237.4,124.7) -- (237.4,77.35) ;
%Straight Lines [id:da01760570202550582] 
\draw    (237.4,77.35) -- (319.2,77.35) ;
%Straight Lines [id:da3751939511907125] 
\draw    (465,124.7) -- (465,77.35) ;
%Straight Lines [id:da29961110180248873] 
\draw    (381.8,77.35) -- (465,77.35) ;

% Text Node
\draw (451.2,144.4) node [anchor=north west][inner sep=0.75pt]  [font=\scriptsize]  {$ \begin{array}{l}
\mathbf{{\displaystyle +}}\\
\mathbf{{\displaystyle -}}
\end{array}$};
% Text Node
\draw (468.6,122.2) node [anchor=north west][inner sep=0.75pt]  [font=\small]  {$V_{amb}$};
% Text Node
\draw (389.8,92.4) node [anchor=north west][inner sep=0.75pt]  [font=\small]  {$R_{\theta SA}$};
% Text Node
\draw (275.8,93.2) node [anchor=north west][inner sep=0.75pt]  [font=\small]  {$R_{\theta HS}$};
% Text Node
\draw (332.2,49.4) node [anchor=north west][inner sep=0.75pt]  [font=\small]  {$R_{\theta HA}$};
% Text Node
\draw (199,121.4) node [anchor=north west][inner sep=0.75pt]  [font=\small]  {$P_{heat}$};
% Text Node
\draw (333.4,99.8) node [anchor=north west][inner sep=0.75pt]  [font=\small]  {$V_{sens}$};
% Text Node
\draw (356.6,129.6) node [anchor=north west][inner sep=0.75pt]  [font=\small]  {$C_{sens}$};

\end{tikzpicture}
\caption{Thermal network model using the electrical circuit elements}
\label{Thermal}
\end{figure}

Later the thermal resistance between the heater and the ambient can be found using again the same technique. Rest of the power flows through the branch 2, that is the upper branch.

\begin{equation}
    I_{power}-I_{branch1}=I_{branch2}
\end{equation}

\begin{equation}
    \frac{V_{heater}-V_{ambient}}{I_{branch2}}=R_{\Theta HA}
\end{equation}

A test voltage of 3.5V is applied to the heater and 0.56 ampere of current is passed resulting in 1.96 watts of power is dissipated on the resistor. From (6) thermal current on branch1 is 0.2033W and on branch2 it is 1.757W. At this stage nickel-chromium wire heated up to 131.5 $\celsius$. Steady state test shows that $R_{\Theta HS}$ is 650 $\celsius$/W, $R_{\Theta HA}$ is 62 $\celsius$/W.

Transient test is applied in order to measure the thermal capacitance. The time constant of the thermal circuit is measured with heating cycle of the system and $C_{sense}$ is measured to be 172 millifarads.

The last test applied in order to fully model the system is the cooling test.The fan effectively reduces the thermal resistance between the temperature sensor and the ambient temperature. For the test the fan is turned on and steady state values of the thermal resistances are measured with constant air flow over the system. Assuming the exiting air velocity is proportional with the motor speed in operation region andair velocity and the convection ratio of the system is in linear relation the thermal resistances are modeled as such\eqref{term}.

\begin{equation}
    R_{\Theta SA}=180-V_{fan}*12
    \label{term}
\end{equation}

\section{Simulation Results}

There are three critical specifications about this project that one can simulate. The first one is that the set and ambient display LEDs must cover the light spectrum with a smooth transition while the set and ambient temperatures cover the whole temperature range (24-40\celsius). The second one is that the fan and the resistor should never act at the same time. Finally, the control and the operation units work effective enough so that the temperature is adjusted rapidly and accurately. The simulations are done on LTspice, the data are exported and plotted in MATLAB. 

To show that the LED currents are as desired, a ramp input is given instead of the temperature measurement to the display unit, and the LED currents are observed in the simulation. Observed current signals are plotted in Fig.~\ref{displaySweep}, which is very close to the desired current signals in Fig.~\ref{ILED}

\begin{figure}
\centerline{}
\caption{Simulated LED currents vs time graphs for each color terminal}
\label{displaySweep}
\end{figure}

To show the other specifications are satisfied, it is needed to model the whole system in LTspice (including the thermal circuit in Fig.~\ref{Thermal}). Fig.~\ref{pwmSim} includes the PWM signals produced for the heater and the fan together. Since they do not intersect, it is concluded that the comparator works as desired.

\begin{figure}
\centerline{}
\caption{Simulated PWM signals for the heater and the fan}
\label{pwmSim}
\end{figure}

Using the same model, Fig.~\ref{pidSim} includes the set and the ambient temperature value waveforms. One can see from Fig.~\ref{pidSim} that the PID controller is able to reduce the error to a desired margin in a reasonable time for our model. Note that this simulation result is only a proof-of-concept showing that PID controller will work in the designed model. The tuning should be done experimentally.

\begin{figure}
\centerline{}
\caption{Simulated set and ambient temperature signals over time}
\label{pidSim}
\end{figure}

\section{Experimental Results}

In the first experiment, the base emitter voltages of the BJTs are measured using an oscilloscope. The results were consistent with the simulation results as expected. The transition was smooth and covering all the range.

In the second experiment, the set and the ambient temperature values are observed on the oscilloscope screen and the data is plotted in Fig.~\ref{pidRise} and Fig.~\ref{pidFall}. One can see that the full temperature can be adjusted and settled to a value very rapidly and accurately. The settling time is around 15 seconds, and the steady state error is strictly less than 1\celsius. As expected from the theoretical knowledge and simulation results, PID method works brilliantly in this specific case.

\begin{figure}
\centerline{}
\caption{Experimental set and ambient temperature signals (rise)}
\label{pidRise}
\end{figure}

\begin{figure}
\centerline{}
\caption{Experimental set and ambient temperature signals (fall)}
\label{pidFall}
\end{figure}

There are no detectable discrepancies with the theoretical and the simulation results, which means the accuracy of the models that are used are very high. Even if there are some deviations, they may be due to the non-idealities of the components and thermal disturbances.

\section{Conclusions}
In this paper, the design and implementation of an autonomous temperature conditioning system is demonstrated. Electrical and thermal systems are modelled in a single simulation environment with feedback loop closed. The PID method is shown that its applicable to this system, but due to the asymmetry of the reverse processes a modified PID circuit is proposed to damp oscillations of the system around the steady state, which is shown to be successful with the experimental results. Moreover, since the control signals are critical for the process, it is observed that filtering the noise with low and high pass filters and also avoiding the EMI effects with a careful PCB design procedure is essential for an accurate and reliable control mechanism.

\begin{thebibliography}{00}
\bibitem{b1} Y. Wu, J. P. Bobis and R. Gehman, "The design and analysis of an improved high air flow meter with analog/digital filters," [1992] Conference Record IEEE Instrumentation and Measurement Technology Conference, 1992, pp. 600-605, doi: 10.1109/IMTC.1992.245068.

\bibitem{b2}Kiam Heong Ang, G. Chong and Yun Li, "PID control system analysis, design, and technology," in IEEE Transactions on Control Systems Technology, vol. 13, no. 4, pp. 559-576, July 2005, doi: 10.1109/TCST.2005.847331.

\bibitem{b3}A. Baskys and V. Zlosnikas, "Asymmetric PID controller," IECON 2006 - 32nd Annual Conference on IEEE Industrial Electronics, 2006, pp. 219-223, doi: 10.1109/IECON.2006.347936.

\bibitem{b4} A. A. Kilov, V. N. Konstantyan, A. S. Sannikov, S. A. Sheptunov and A. A. Chetvertakov, "Applying Digital Filters to Suppress Noise in the Derivative Term of the PID Controller," 2021 International Conference on Quality Management, Transport and Information Security, Information Technologies (IT&QM&IS), 2021, pp. 301-304, doi: 10.1109/ITQMIS53292.2021.9642889.

\end{thebibliography}
\end{document}

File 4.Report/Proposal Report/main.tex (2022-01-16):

% Template last modified by Jake Hart; please contact course staff if you have any questions regarding using this template

\documentclass{METUHW} % You must have the cisXXX .cls file in your project or working directory (i.e. the same directory as this document) 
\HWno{1} % Enter the number of the homework you are working on
\HWcourse{EE313} % Enter the course department and number here
\HWpartner{Özgür Gülsuna} % If your class allows group work, put your partners here
\usepackage{amsmath}
\usepackage{calc}
\usepackage{xcolor}\pagecolor{white}
\usepackage[linguistics]{forest}
\usepackage{listings}[language=matlab]
\usepackage{listings}
\usepackage{color}
\usepackage{xcolor}
\usepackage[colorinlistoftodos]{todonotes}
\usepackage{float}
\usepackage{circuitikz}
\usepackage{ragged2e}
\usepackage{steinmetz}

%includes for tikz
\usepackage{physics}
\usepackage{amsmath}
\usepackage{tikz}
\usepackage{mathdots}
\usepackage{yhmath}
\usepackage{cancel}
\usepackage{color}
\usepackage{siunitx}
\usepackage{array}
\usepackage{multirow}
\usepackage{amssymb}
\usepackage{gensymb}
\usepackage{tabularx}
\usepackage{extarrows}
\usepackage{booktabs}
\usetikzlibrary{fadings}
\usetikzlibrary{patterns}
\usetikzlibrary{shadows.blur}
\usetikzlibrary{shapes}

\usepackage{physics}
\usepackage{amsmath}
\usepackage{tikz}
\usepackage{mathdots}
\usepackage{yhmath}
\usepackage{cancel}
\usepackage{color}
\usepackage{siunitx}
\usepackage{array}
\usepackage{multirow}
\usepackage{amssymb}
\usepackage{gensymb}
\usepackage{tabularx}
\usepackage{extarrows}
\usepackage{booktabs}
\usetikzlibrary{fadings}
\usetikzlibrary{patterns}
\usetikzlibrary{shadows.blur}
\usetikzlibrary{shapes}

\restylefloat{table}

\definecolor{codegreen}{rgb}{0,0.5,0.5}
\definecolor{codegray}{rgb}{0.5,0.5,0.5}
\definecolor{codepurple}{rgb}{0.6,0.1,0.1}
\definecolor{backcolour}{rgb}{0.95,0.95,0.95}

\lstdefinestyle{mystyle}{
    backgroundcolor=\color{backcolour},   
    commentstyle=\color{codegreen},
    keywordstyle=\color{magenta},
    numberstyle=\tiny\color{codegray},
    stringstyle=\color{codepurple},
    basicstyle=\ttfamily\footnotesize,
    breakatwhitespace=false,         
    breaklines=true,                 
    captionpos=b,                    
    keepspaces=true,                 
    numbers=false,                    
    numbersep=5pt,                  
    showspaces=false,                
    showstringspaces=false,
    showtabs=false,                  
    tabsize=2
}

\lstset{style=mystyle}

\newcommand*{\CenterVdots}{\makebox[\widthof{(0,0),}][c]{\vdots}}

\begin{document}

\title{{%   <-- starts a group
\vspace{-3cm}
\scriptsize
\normalsize
\textbf{EE313 ANALOG ELECTRONICS LABORATORY \\ \small TERM PROJECT}\\
\large\\
}%   <-- ends that group

\textbf{
PROPOSAL REPORT\\
}
\small
Design of a Micro-Air Conditioner\\
\medskip
\medskip
\medskip
\small

Özgür Gülsuna 2307668 \hfill 16.01.2022\\
\raggedright
Işık Emir Altunkol 2442408 \hfill Time Spent: 12 hours

}

\author{ }
\date{ }
\maketitle

\vspace{-4em}

\justifying

    To design an air conditioning system, we need to have a sensing unit, display unit, control unit, and an operation unit. In this document, we will explain our approach to implement those functioning units one by one. \\
\medskip

\textbf{ \normalsize Sensing Unit}\\
\fontsğze
    Sensing unit is a simple unit consisting of a temperature sensor and its amplifier. For the actual sensor we are going to use LM35. It will give a voltage output which has a linear relation with the temperature in the specified range. Some of the other features of this sensor are, 4-30 V operation range and 0.5°C accuracy. Amplifier at the output of the temperature sensor will enable us to isolate the different parts of the circuit which ensure its reliability and it will help us to scale the reading to a more useful range. We will place the sensor close enough to the heating and cooling elements so that we can change the temperature at the desired rate.\\

\medskip

\textbf{ \normalsize Display Unit}\\
    Display unit consists of two sets of RGB LEDs (red-green-blue light emitting diodes) in common anode configuration - one for displaying the set value, and the other for displaying the measured room temperature. We wanted to separate the LEDs to better visualize the operation of the system. As described in the project, we have a color bar indicating the temperatures. To achieve the same output we need to create three different signals for each LED.  Required signal for each color is shown in Figure 1. Series of operational amplifier structures will be used to generate the aforementioned signal. When it comes to driving the LEDs we will utilize bipolar junction transistors (BJTs). These semiconductor devices enable us to control the current of the individual LEDs which corresponds to their brightness. The selected topology is a common emitter amplifier. This structure is also named as  transconductance amplifier, which means that an input voltage produces an output current.

\begin{figure}[H]
\centering
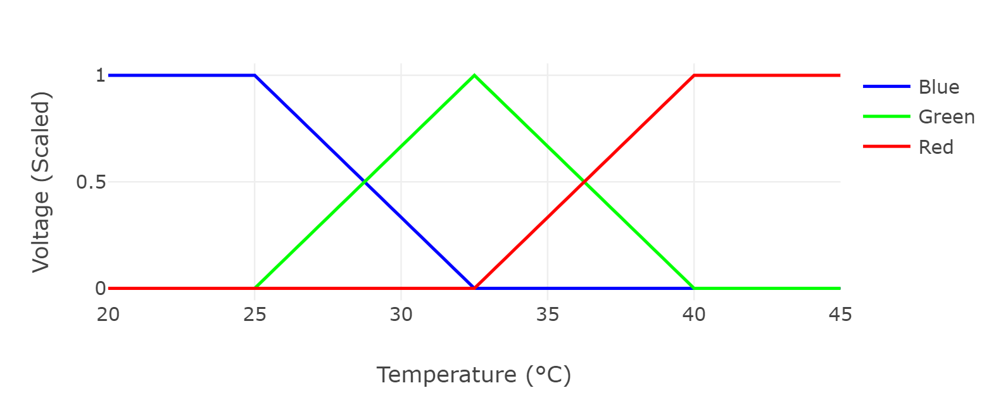
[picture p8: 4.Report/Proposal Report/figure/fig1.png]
\\
\centering
Figure 1. LED driving signals for each color.
\end{figure}

\textbf{ \normalsize Control Unit}\\
    Control unit has the highest complexity among others. It will have several parts for handling various tasks. First of all, it will take input from two different sources. First one will be the amplified output voltage of the temperature sensor. Second one will be the reading from the potentiometer. This unit will generate outputs for two different elements, heating and cooling respectively. We decided to implement a PID (proportional integral derivative) controller for this task, which is a controller with feedback. This way we can control the elements in an analogous fashion. We will take the input from the potentiometer as the set point and the amplified LM35 output as the process variable. The PID implementation will be done with operational amplifier configurations as shown in Figure 2. For op-amp selection, we will go with LM358 dual channel op-amps. They are cheap, reliable and suitable for the control unit. Also a dead-band is constructed at the end of this stage.

\centering

\tikzset{every picture/.style={line width=0.75pt}} %set default line width to 0.75pt        

\begin{tikzpicture}[x=0.75pt,y=0.75pt,yscale=-1,xscale=1]
%uncomment if require: \path (0,208); %set diagram left start at 0, and has height of 208

%Shape: Resistor [id:dp8858278922494136] 
\draw   (174.26,88.32) -- (190.4,88.32) -- (193.99,77.25) -- (201.16,99.39) -- (208.33,77.25) -- (215.5,99.39) -- (222.68,77.25) -- (229.85,99.39) -- (237.02,77.25) -- (244.19,99.39) -- (247.78,88.32) -- (263.92,88.32) ;
%Shape: Capacitor [id:dp03371552137820011] 
\draw   (168.33,41.69) -- (216.02,41.69) (226.61,20.5) -- (226.61,62.89) (216.02,20.5) -- (216.02,62.89) (226.61,41.69) -- (274.3,41.69) ;
%Shape: Triangle [id:dp98497243420744] 
\draw  [fill={rgb, 255:red, 217; green, 217; blue, 217 }  ,fill opacity=1 ] (394.24,102.94) -- (335.76,136.52) -- (335.76,69.35) -- cycle ;
%Straight Lines [id:da3971318773795933] 
\draw    (168.33,41.69) -- (168.33,88.32) ;
%Straight Lines [id:da3049997475460431] 
\draw    (274.3,41.69) -- (274.3,88.32) ;
%Straight Lines [id:da7159809408880349] 
\draw    (274.3,88.32) -- (335.34,88.32) ;
%Straight Lines [id:da9186521041305018] 
\draw    (174.26,88.32) -- (168.33,88.32) ;
%Straight Lines [id:da0908787872310326] 
\draw    (263.92,88.32) -- (274.3,88.32) ;
%Shape: Resistor [id:dp13518795960649532] 
\draw   (295.49,41.69) -- (311.63,41.69) -- (315.22,30.62) -- (322.39,52.77) -- (329.56,30.62) -- (336.73,52.77) -- (343.91,30.62) -- (351.08,52.77) -- (358.25,30.62) -- (365.42,52.77) -- (369.01,41.69) -- (385.15,41.69) ;
%Straight Lines [id:da3878971923579282] 
\draw    (295.49,41.69) -- (295.49,88.32) ;
%Shape: Capacitor [id:dp1987350161026391] 
\draw   (385.15,41.69) -- (432.83,41.69) (443.43,20.5) -- (443.43,62.89) (432.83,20.5) -- (432.83,62.89) (443.43,41.69) -- (491.12,41.69) ;
%Straight Lines [id:da7857458487620923] 
\draw    (394.24,102.94) -- (515.13,102.94) ;
%Straight Lines [id:da3195712557469328] 
\draw    (491.12,41.69) -- (491.12,102.94) ;
%Straight Lines [id:da9218474418090266] 
\draw    (295.49,115.87) -- (295.49,162.5) ;
%Straight Lines [id:da3520350954534184] 
\draw    (295.49,115.87) -- (335.88,115.87) ;
%Straight Lines [id:da9046341306409746] 
\draw    (295.49,162.5) -- (148.77,162.5) ;
%Straight Lines [id:da6420173241490861] 
\draw    (515.13,162.5) -- (295.49,162.5) ;
%Straight Lines [id:da18257571009246387] 
\draw    (168.33,88.32) -- (148.77,88.32) ;
%Flowchart: Connector [id:dp0488086244709538] 
\draw   (142.84,88.32) .. controls (142.84,86.68) and (144.17,85.35) .. (145.8,85.35) .. controls (147.44,85.35) and (148.77,86.68) .. (148.77,88.32) .. controls (148.77,89.96) and (147.44,91.29) .. (145.8,91.29) .. controls (144.17,91.29) and (142.84,89.96) .. (142.84,88.32) -- cycle ;
%Flowchart: Connector [id:dp7782162243873112] 
\draw   (142.84,162.5) .. controls (142.84,160.86) and (144.17,159.53) .. (145.8,159.53) .. controls (147.44,159.53) and (148.77,160.86) .. (148.77,162.5) .. controls (148.77,164.14) and (147.44,165.47) .. (145.8,165.47) .. controls (144.17,165.47) and (142.84,164.14) .. (142.84,162.5) -- cycle ;
%Flowchart: Connector [id:dp7350444455171572] 
\draw   (515.13,162.5) .. controls (515.13,160.86) and (516.45,159.53) .. (518.09,159.53) .. controls (519.73,159.53) and (521.06,160.86) .. (521.06,162.5) .. controls (521.06,164.14) and (519.73,165.47) .. (518.09,165.47) .. controls (516.45,165.47) and (515.13,164.14) .. (515.13,162.5) -- cycle ;
%Flowchart: Connector [id:dp4930242403173162] 
\draw   (515.13,102.94) .. controls (515.13,101.3) and (516.45,99.97) .. (518.09,99.97) .. controls (519.73,99.97) and (521.06,101.3) .. (521.06,102.94) .. controls (521.06,104.58) and (519.73,105.9) .. (518.09,105.9) .. controls (516.45,105.9) and (515.13,104.58) .. (515.13,102.94) -- cycle ;

% Text Node
\draw (339.35,106.62) node [anchor=north west][inner sep=0.75pt]   [align=left] {+};
% Text Node
\draw (341.37,77.77) node [anchor=north west][inner sep=0.75pt]   [align=left] {{\large -}};
% Text Node
\draw (205.6,103.2) node [anchor=north west][inner sep=0.75pt]    {$R_{1}$};
% Text Node
\draw (326.8,7.4) node [anchor=north west][inner sep=0.75pt]    {$R_{2}$};
% Text Node
\draw (189.2,8) node [anchor=north west][inner sep=0.75pt]    {$C_{1}$};
% Text Node
\draw (408.8,6.2) node [anchor=north west][inner sep=0.75pt]    {$C_{2}$};
% Text Node
\draw (140.8,122.8) node [anchor=north west][inner sep=0.75pt]    {$V_{in}$};
% Text Node
\draw (496,120.8) node [anchor=north west][inner sep=0.75pt]    {$V_{out}$};

\end{tikzpicture}

\\

\centering
Figure 2. PID controller implemented with single operational amplifier.\\

\medskip

\raggedright

\justifying

\textbf{ \normalsize Operation Unit}\\
    Operation unit is sort of a driver unit. In this section, output of the control unit is picked up and converted into pulse width modulation (PWM) signals so that our elements can be controlled more accurately. An oscillator will be implemented in this section to generate the PWM clock for the elements. This single clock will be utilized by both of the comparator blocks, which means that their frequency will be the same. Basically the triangle oscillator is compared with control signals to generate desired PWM signals for each output. Later these signals are fed onto mosfet bridges to adjust the power given to each element. The heating element is selected as a piece of nickel-chromium wire. The heating wire will be wrapped around our temperature sensor without touching to ensure more of the power is transferred onto the sensor. The resistance value for the wire will be chosen such that at most it will dissipate 10 watts of power. For cooling we will use a 12 V computer fan, which takes direct current voltage for an input. The power consumption of the selected fan is around 2 watts. Preliminary experiments showed that these power ratings will be fairly enough.\\
    
\medskip

\textbf{ \normalsize Mechanical Design}\\
Mechanical construction of the system is decided to be built upon the fan. The mounting holes of the fan will be used to carry the circuit and the sensor will be placed on the circuit and directed towards the fan and it will be surrounded by the heating wire. For this design our circuit will be carried over the printed circuit board (PCB) with surface mount components. KiCad is selected for the PCB drawing program since it is open source and easy to use . This approach not only shrinks the size of the circuit but also helps us to reduce the electromagnetic interference. In the end we hope this rigid construction will be aesthetically pleasing (see Figure 3).\\

\begin{figure}[H]
\centering

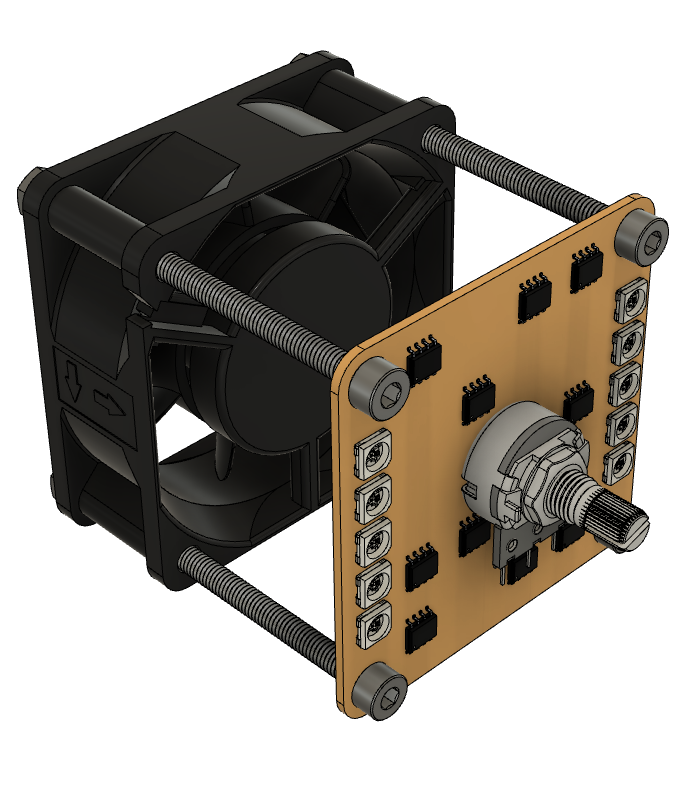
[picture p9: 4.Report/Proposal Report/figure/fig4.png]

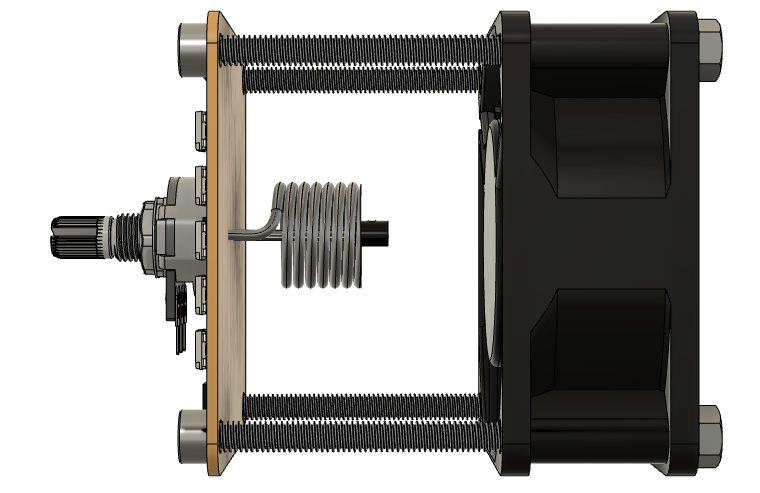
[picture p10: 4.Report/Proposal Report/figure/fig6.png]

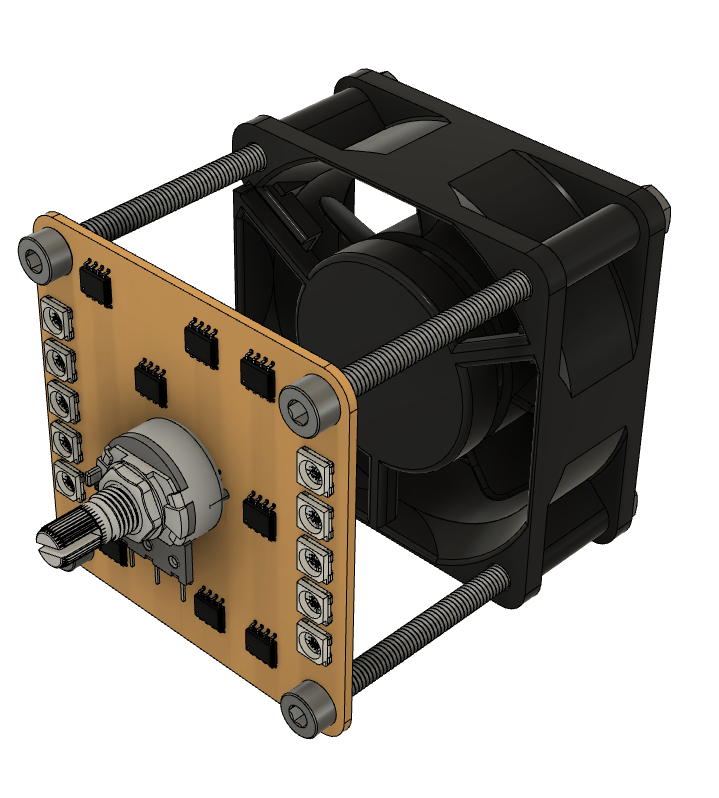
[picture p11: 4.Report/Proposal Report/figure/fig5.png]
\\
\centering
Figure 3. Computer aided drawing of the planned construct.
\end{figure}

\\

	As we work on this project, we will first precisely choose the components we use (with their values) and simulate our designs in LTspice by simulating each unit separately and simulating some of them together (if applicable). If we get the results we expected, we will move on to the prototyping stage where we build each unit on a breadboard and test them. After all these stages, the circuit is reconstructed on a PCB and mounted on the fan.
	
\vspace{-2em}

 \end{document}

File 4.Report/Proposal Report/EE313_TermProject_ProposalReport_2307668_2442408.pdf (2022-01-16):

EE313 ANALOG ELECTRONICS LABORATORY TERM PROJECT

# PROPOSAL REPORT

Design of a Micro-Air Conditioner

Ozg¨ur G¨ulsuna 2307668 ¨ | 16.01.2022
I¸sık Emir Altunkol 2442408 | Time Spent: 12 hours

To design an air conditioning system, we need to have a sensing unit, display unit, control unit, and an operation unit. In this document, we will explain our approach to implement those functioning units one by one.

Sensing Unit
Sensing unit is a simple unit consisting of a temperature sensor and its amplifier. For the actual sensor we are going to use LM35. It will give a voltage output which has a linear relation with the temperature in the specified range. Some of the other features of this sensor are, 4-30 V operation range and 0.5°C accuracy. Amplifier at the output of the temperature sensor will enable us to isolate the different parts of the circuit which ensure its reliability and it will help us to scale the reading to a more useful range. We will place the sensor close enough to the heating and cooling elements so that we can change the temperature at the desired rate.

Display Unit
Display unit consists of two sets of RGB LEDs (red-green-blue light emitting diodes) in common anode configuration - one for displaying the set value, and the other for displaying the measured room temperature. We wanted to separate the LEDs to better visualize the operation of the system. As described in the project, we have a color bar indicating the temperatures. To achieve the same output we need to create three different signals for each LED. Required signal for each color is shown in Figure 1. Series of operational amplifier structures will be used to generate the aforementioned signal. When it comes to driving the LEDs we will utilize bipolar junction transistors (BJTs). These semiconductor devices enable us to control the current of the individual LEDs which corresponds to their brightness. The selected topology is a common emitter amplifier. This structure is also named as transconductance amplifier, which means that an input voltage produces an output current.


Figure 1. LED driving signals for each color.

Control Unit
Control unit has the highest complexity among others. It will have several parts for handling various tasks. First of all, it will take input from two different sources. First one will be the amplified output voltage of the temperature sensor. Second one will be the reading from the potentiometer. This unit will generate outputs for two different elements, heating and cooling respectively. We decided to implement a PID (proportional integral derivative) controller for this task, which is a controller with feedback. This way we can control the elements in an analogous fashion. We will take the input from the potentiometer as the set point and the amplified LM35 output as the process variable. The PID implementation will be done with operational amplifier configurations as shown in Figure 2. For op-amp selection, we will go with LM358 dual channel op-amps. They are cheap, reliable and suitable for the control unit. Also a dead-band is constructed at the end of this stage.

1

Proposal Report | EE313 | Fall 2021-2022

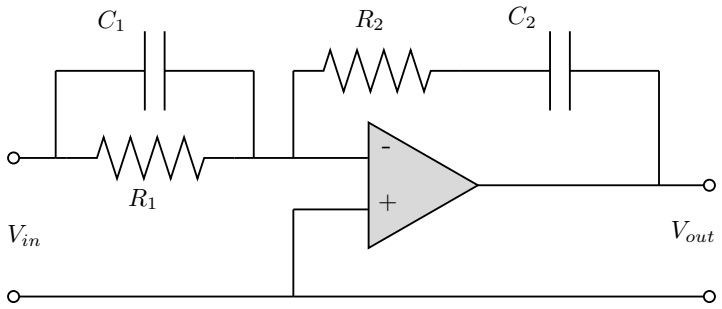
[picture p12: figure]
Vin; Vout

Figure 2. PID controller implemented with single operational amplifier.

Operation Unit
Operation unit is sort of a driver unit. In this section, output of the control unit is picked up and converted into pulse width modulation (PWM) signals so that our elements can be controlled more accurately. An oscillator will be implemented in this section to generate the PWM clock for the elements. This single clock will be utilized by both of the comparator blocks, which means that their frequency will be the same. Basically the triangle oscillator is compared with control signals to generate desired PWM signals for each output. Later these signals are fed onto mosfet bridges to adjust the power given to each element. The heating element is selected as a piece of nickel-chromium wire. The heating wire will be wrapped around our temperature sensor without touching to ensure more of the power is transferred onto the sensor. The resistance value for the wire will be chosen such that at most it will dissipate 10 watts of power. For cooling we will use a 12 V computer fan, which takes direct current voltage for an input. The power consumption of the selected fan is around 2 watts. Preliminary experiments showed that these power ratings will be fairly enough.

Mechanical Design
Mechanical construction of the system is decided to be built upon the fan. The mounting holes of the fan will be used to carry the circuit and the sensor will be placed on the circuit and directed towards the fan and it will be surrounded by the heating wire. For this design our circuit will be carried over the printed circuit board (PCB) with surface mount components. KiCad is selected for the PCB drawing program since it is open source and easy to use . This approach not only shrinks the size of the circuit but also helps us to reduce the electromagnetic interference. In the end we hope this rigid construction will be aesthetically pleasing (see Figure 3).

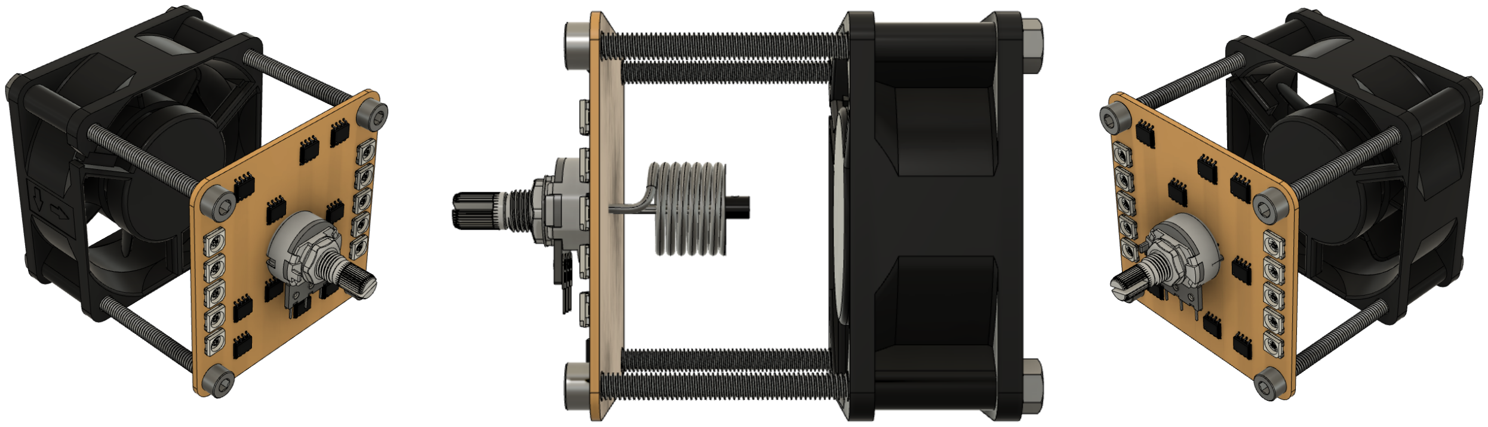
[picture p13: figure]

Figure 3. Computer aided drawing of the planned construct.

As we work on this project, we will first precisely choose the components we use (with their values) and simulate our designs in LTspice by simulating each unit separately and simulating some of them together (if applicable). If we get the results we expected, we will move on to the prototyping stage where we build each unit on a breadboard and test them. After all these stages, the circuit is reconstructed on a PCB and mounted on the fan.

2

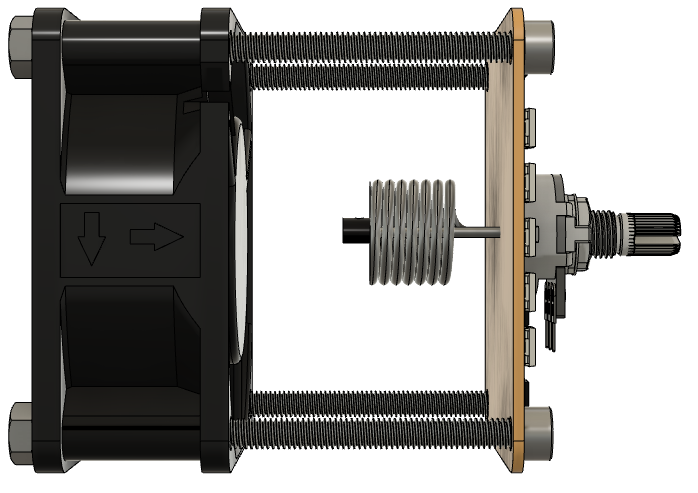
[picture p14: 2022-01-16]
4.Report/Proposal Report/figure/fig3.png

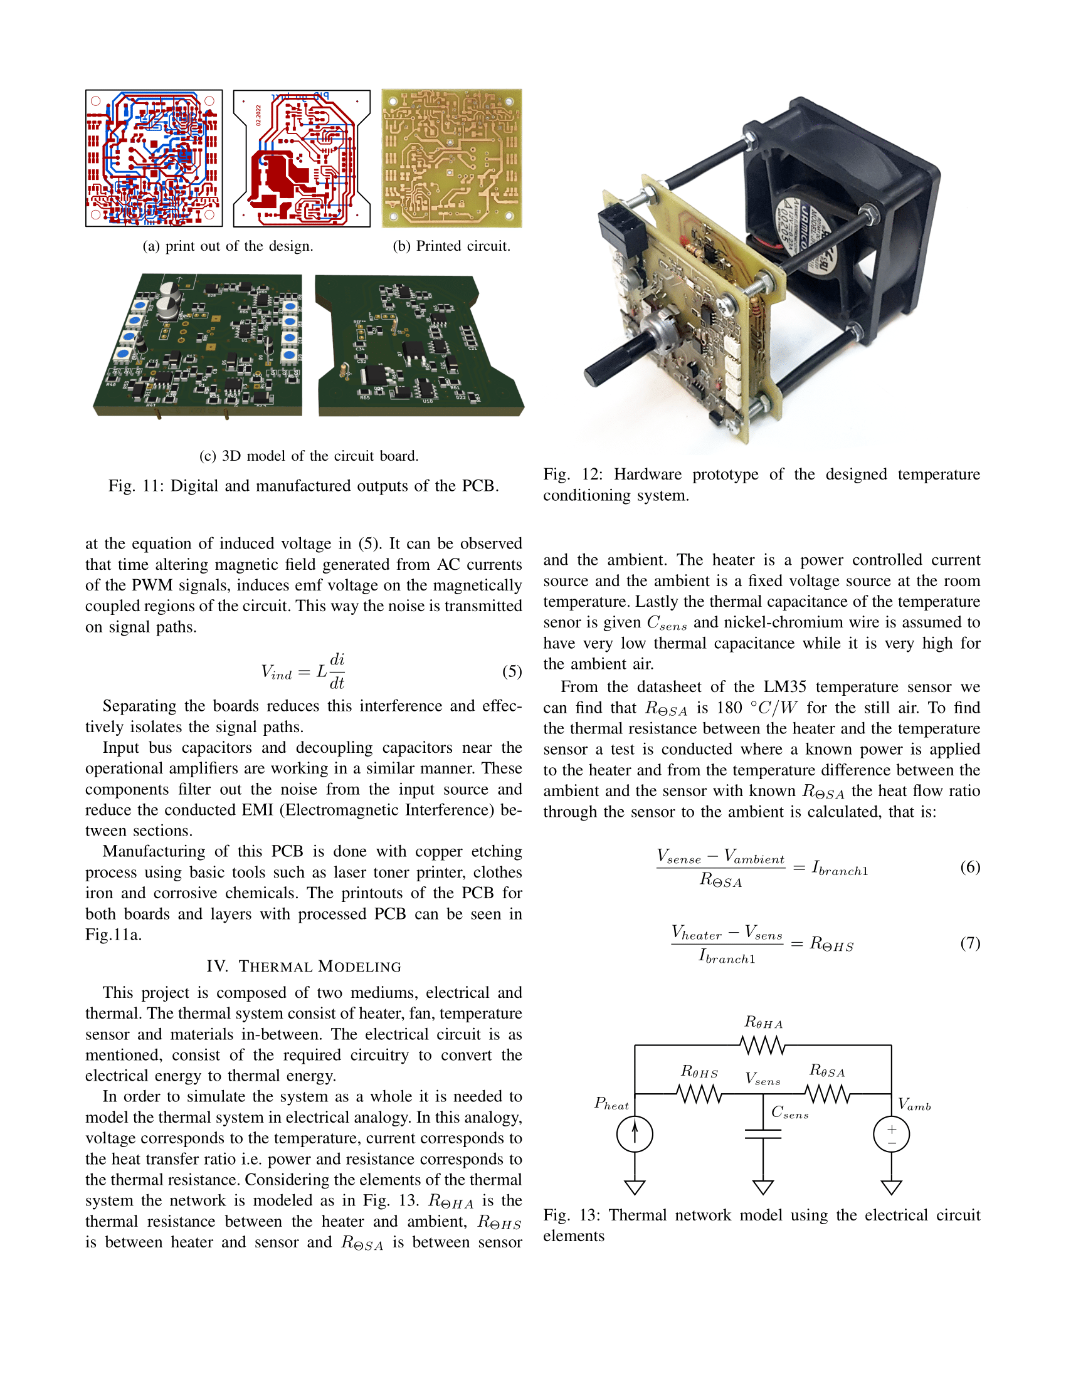
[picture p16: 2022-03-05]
4.Report/Final Report/png/readme5.png

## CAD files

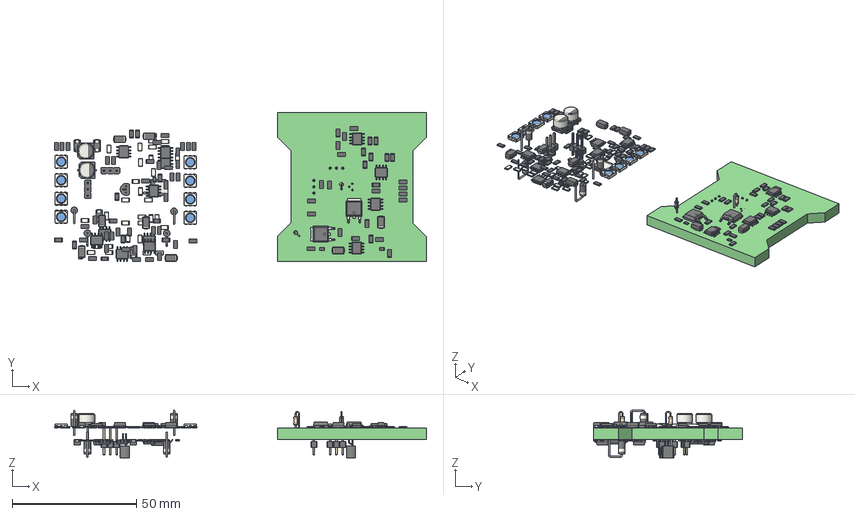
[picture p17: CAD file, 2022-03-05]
2.Hardware/3D model/PCBs.step
149.7 x 60.1 x 19.2 mm
_autosave-v2 PCB

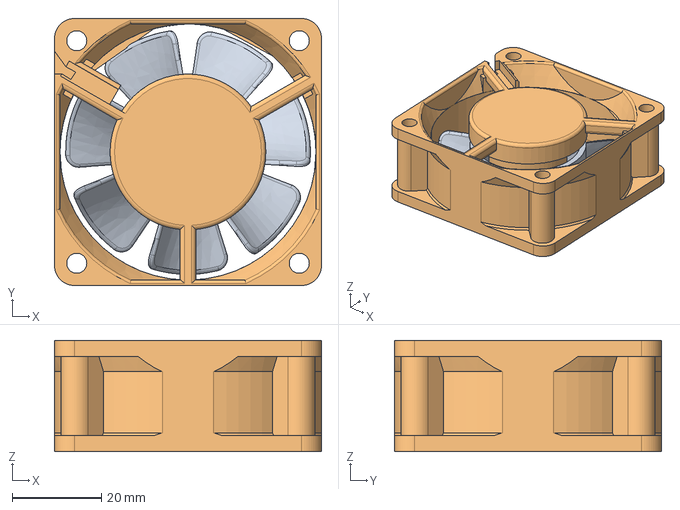
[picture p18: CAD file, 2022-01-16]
2.Hardware/3D model/Fan 60x60x25mm.stp
60.0 x 60.0 x 25.0 mm

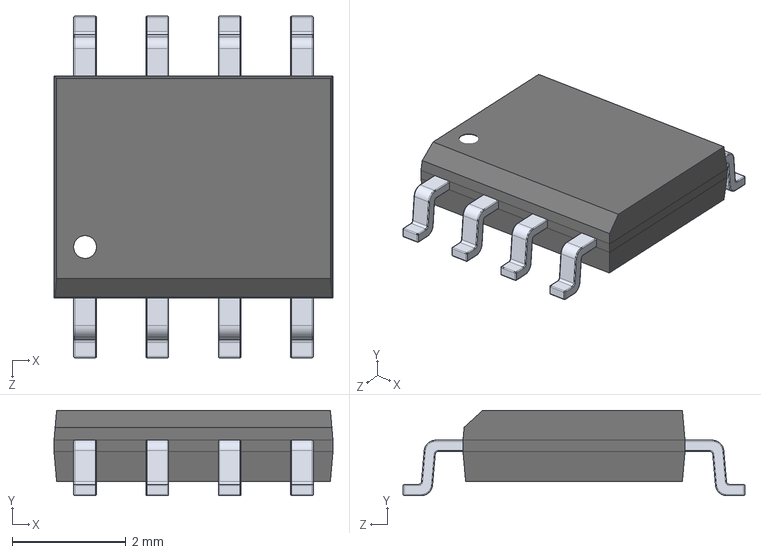
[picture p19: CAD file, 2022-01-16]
2.Hardware/3D model/Package, SOIC-8, 3.9mm.STEP
4.90 x 1.50 x 6.00 mm

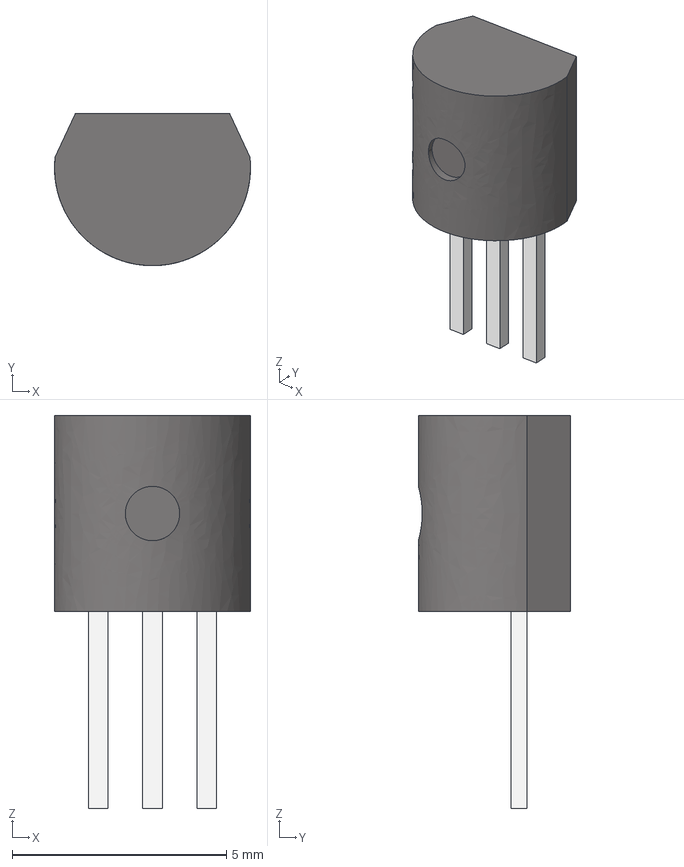
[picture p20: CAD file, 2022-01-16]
2.Hardware/3D model/TO-92.stp
4.58 x 3.56 x 9.18 mm

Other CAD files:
2.Hardware/3D model/WS2812B.f3d

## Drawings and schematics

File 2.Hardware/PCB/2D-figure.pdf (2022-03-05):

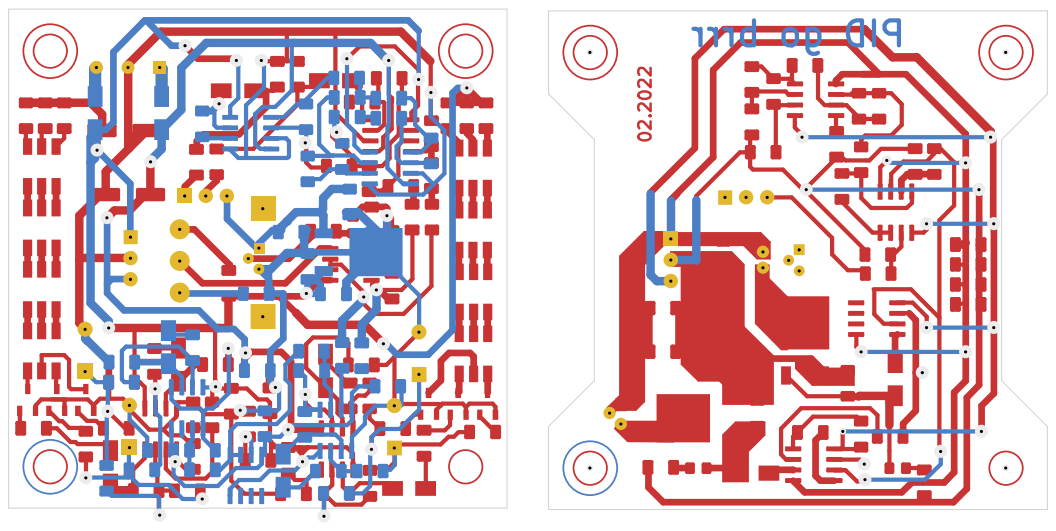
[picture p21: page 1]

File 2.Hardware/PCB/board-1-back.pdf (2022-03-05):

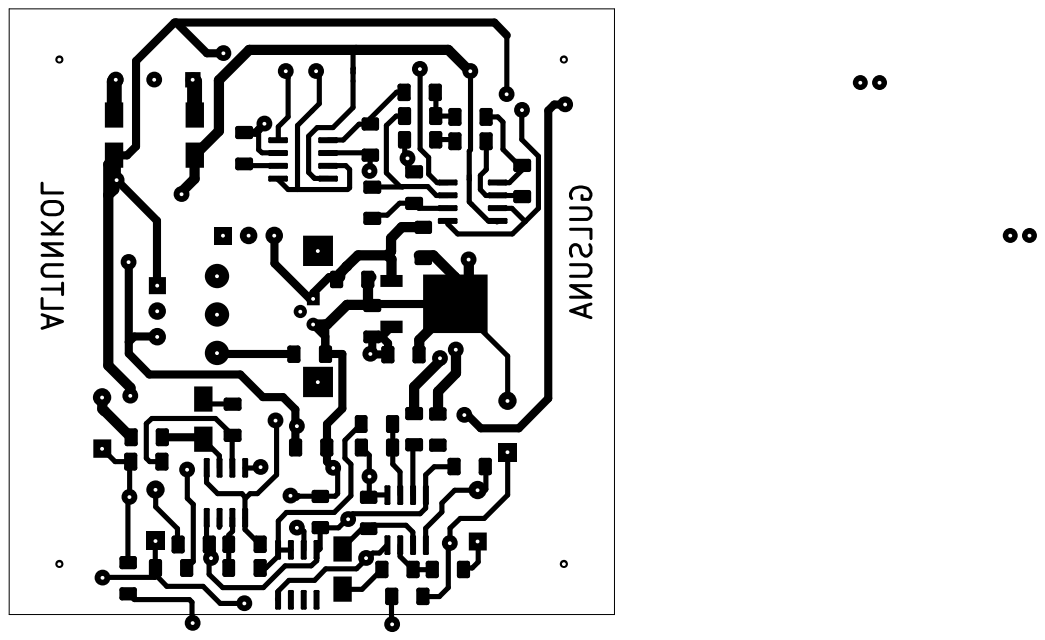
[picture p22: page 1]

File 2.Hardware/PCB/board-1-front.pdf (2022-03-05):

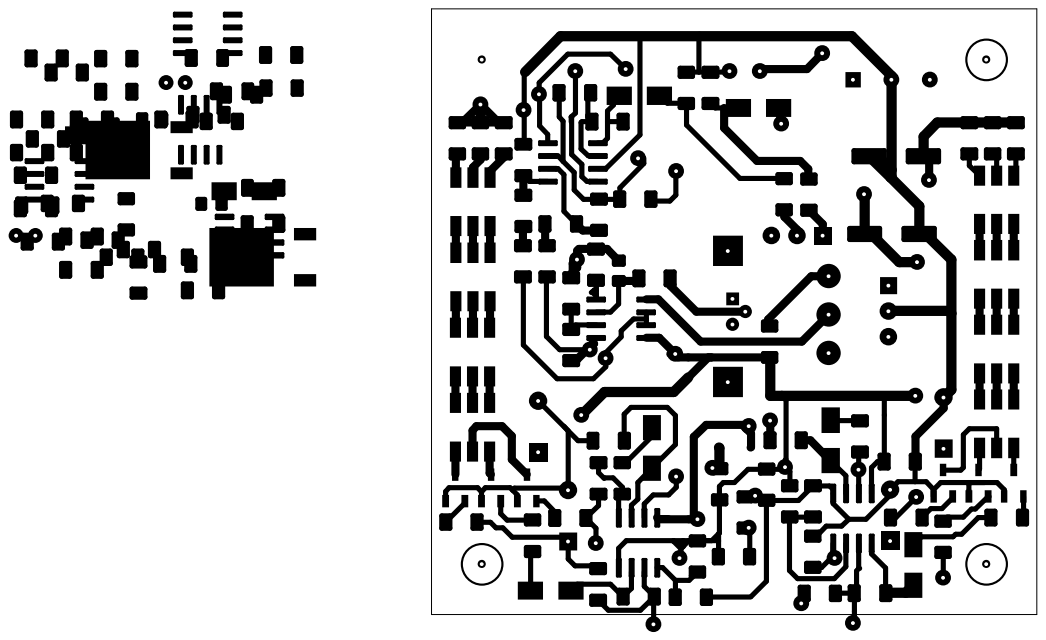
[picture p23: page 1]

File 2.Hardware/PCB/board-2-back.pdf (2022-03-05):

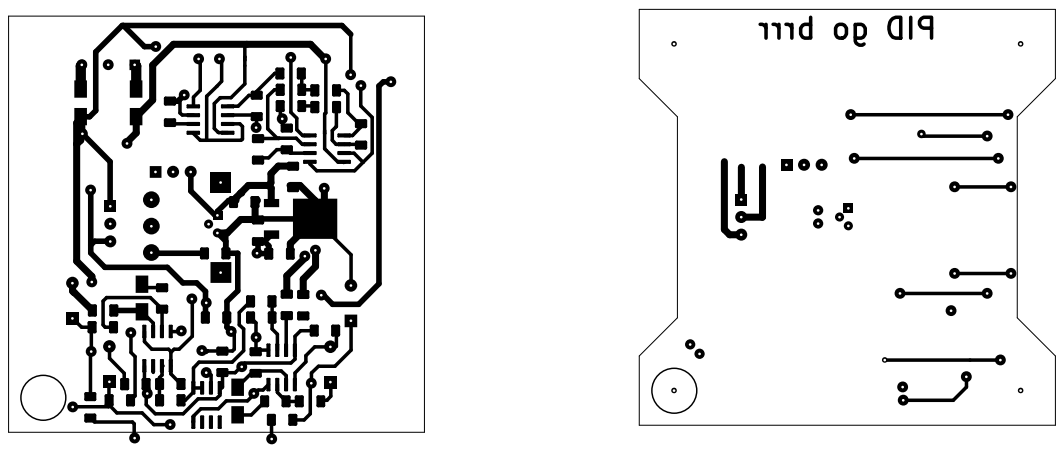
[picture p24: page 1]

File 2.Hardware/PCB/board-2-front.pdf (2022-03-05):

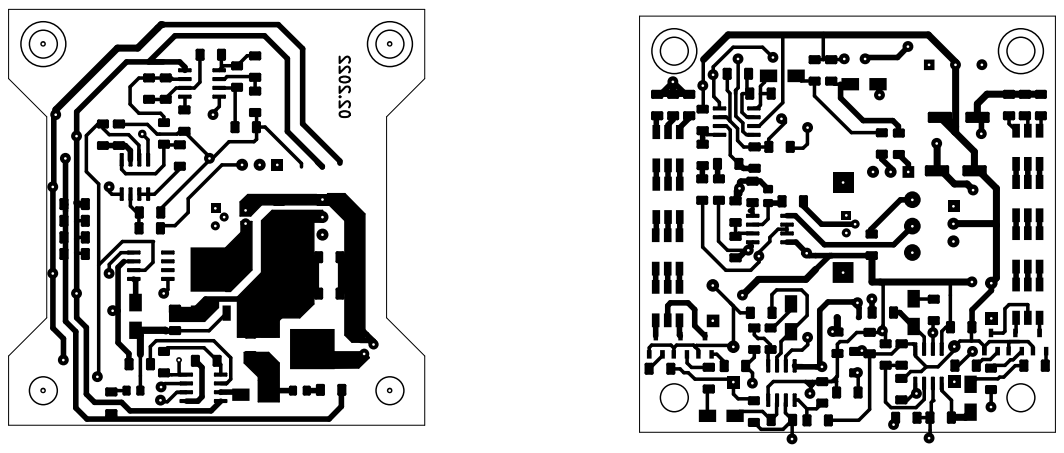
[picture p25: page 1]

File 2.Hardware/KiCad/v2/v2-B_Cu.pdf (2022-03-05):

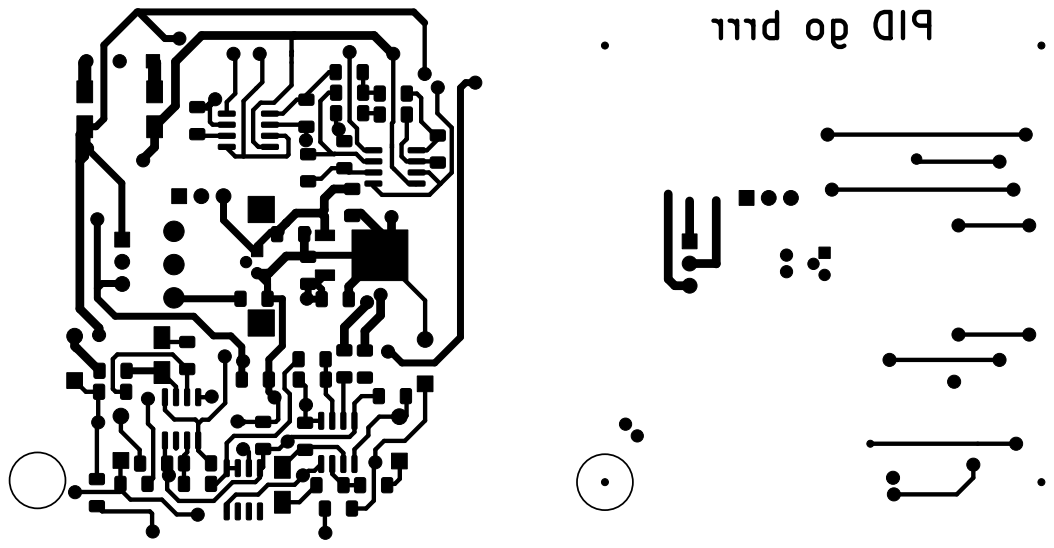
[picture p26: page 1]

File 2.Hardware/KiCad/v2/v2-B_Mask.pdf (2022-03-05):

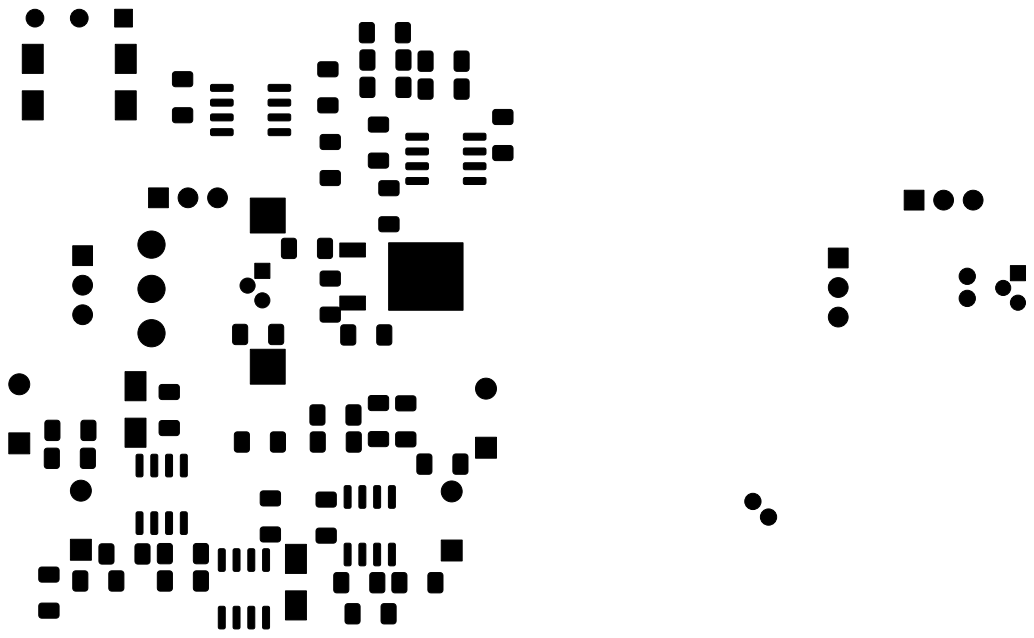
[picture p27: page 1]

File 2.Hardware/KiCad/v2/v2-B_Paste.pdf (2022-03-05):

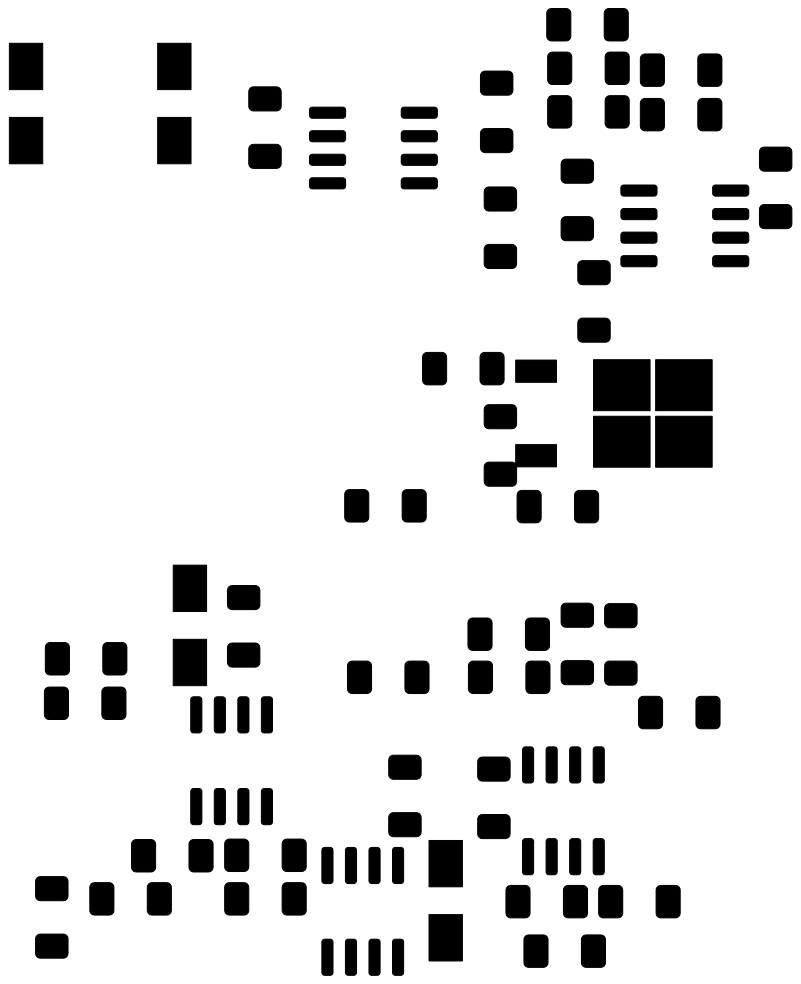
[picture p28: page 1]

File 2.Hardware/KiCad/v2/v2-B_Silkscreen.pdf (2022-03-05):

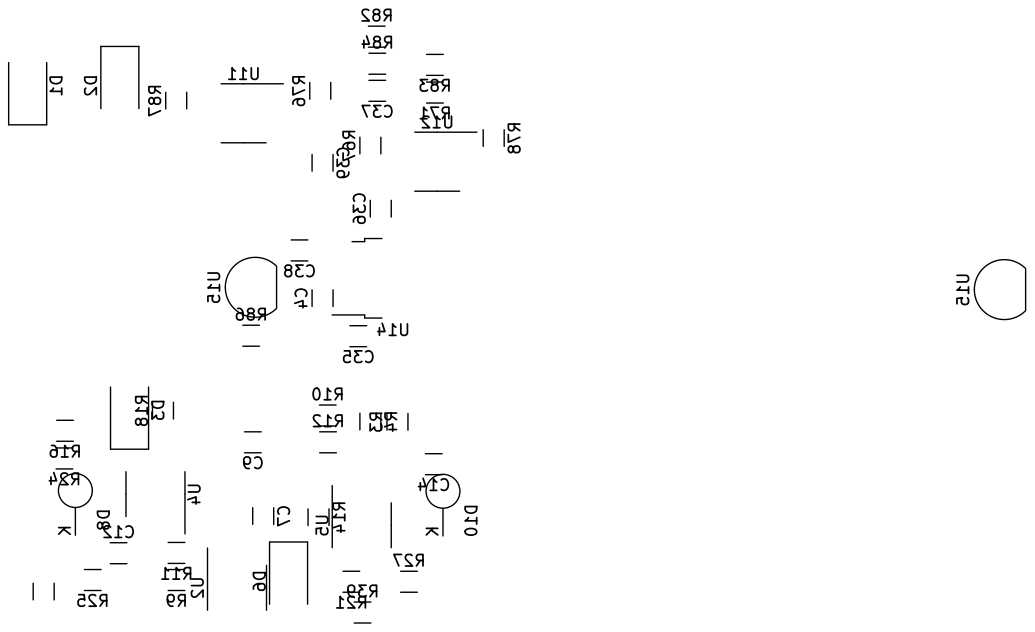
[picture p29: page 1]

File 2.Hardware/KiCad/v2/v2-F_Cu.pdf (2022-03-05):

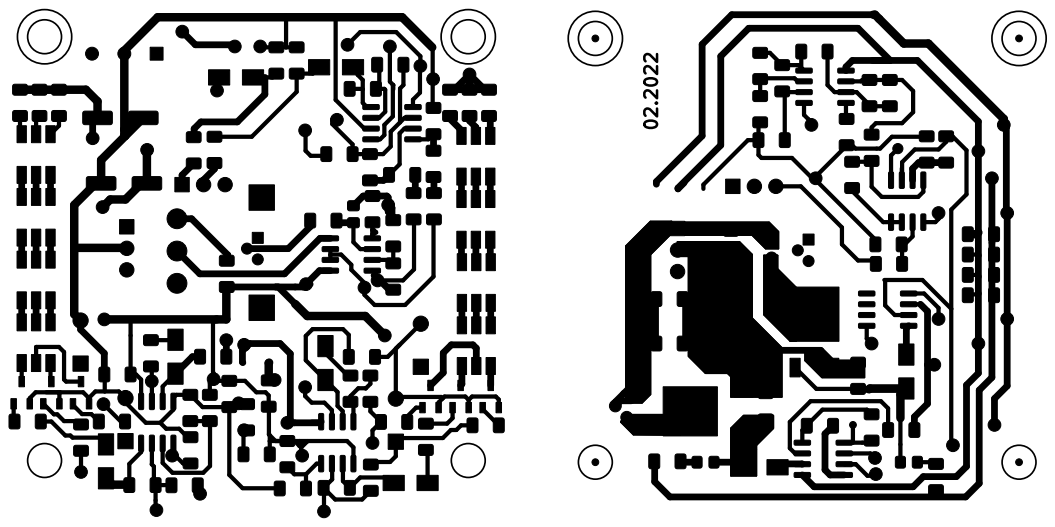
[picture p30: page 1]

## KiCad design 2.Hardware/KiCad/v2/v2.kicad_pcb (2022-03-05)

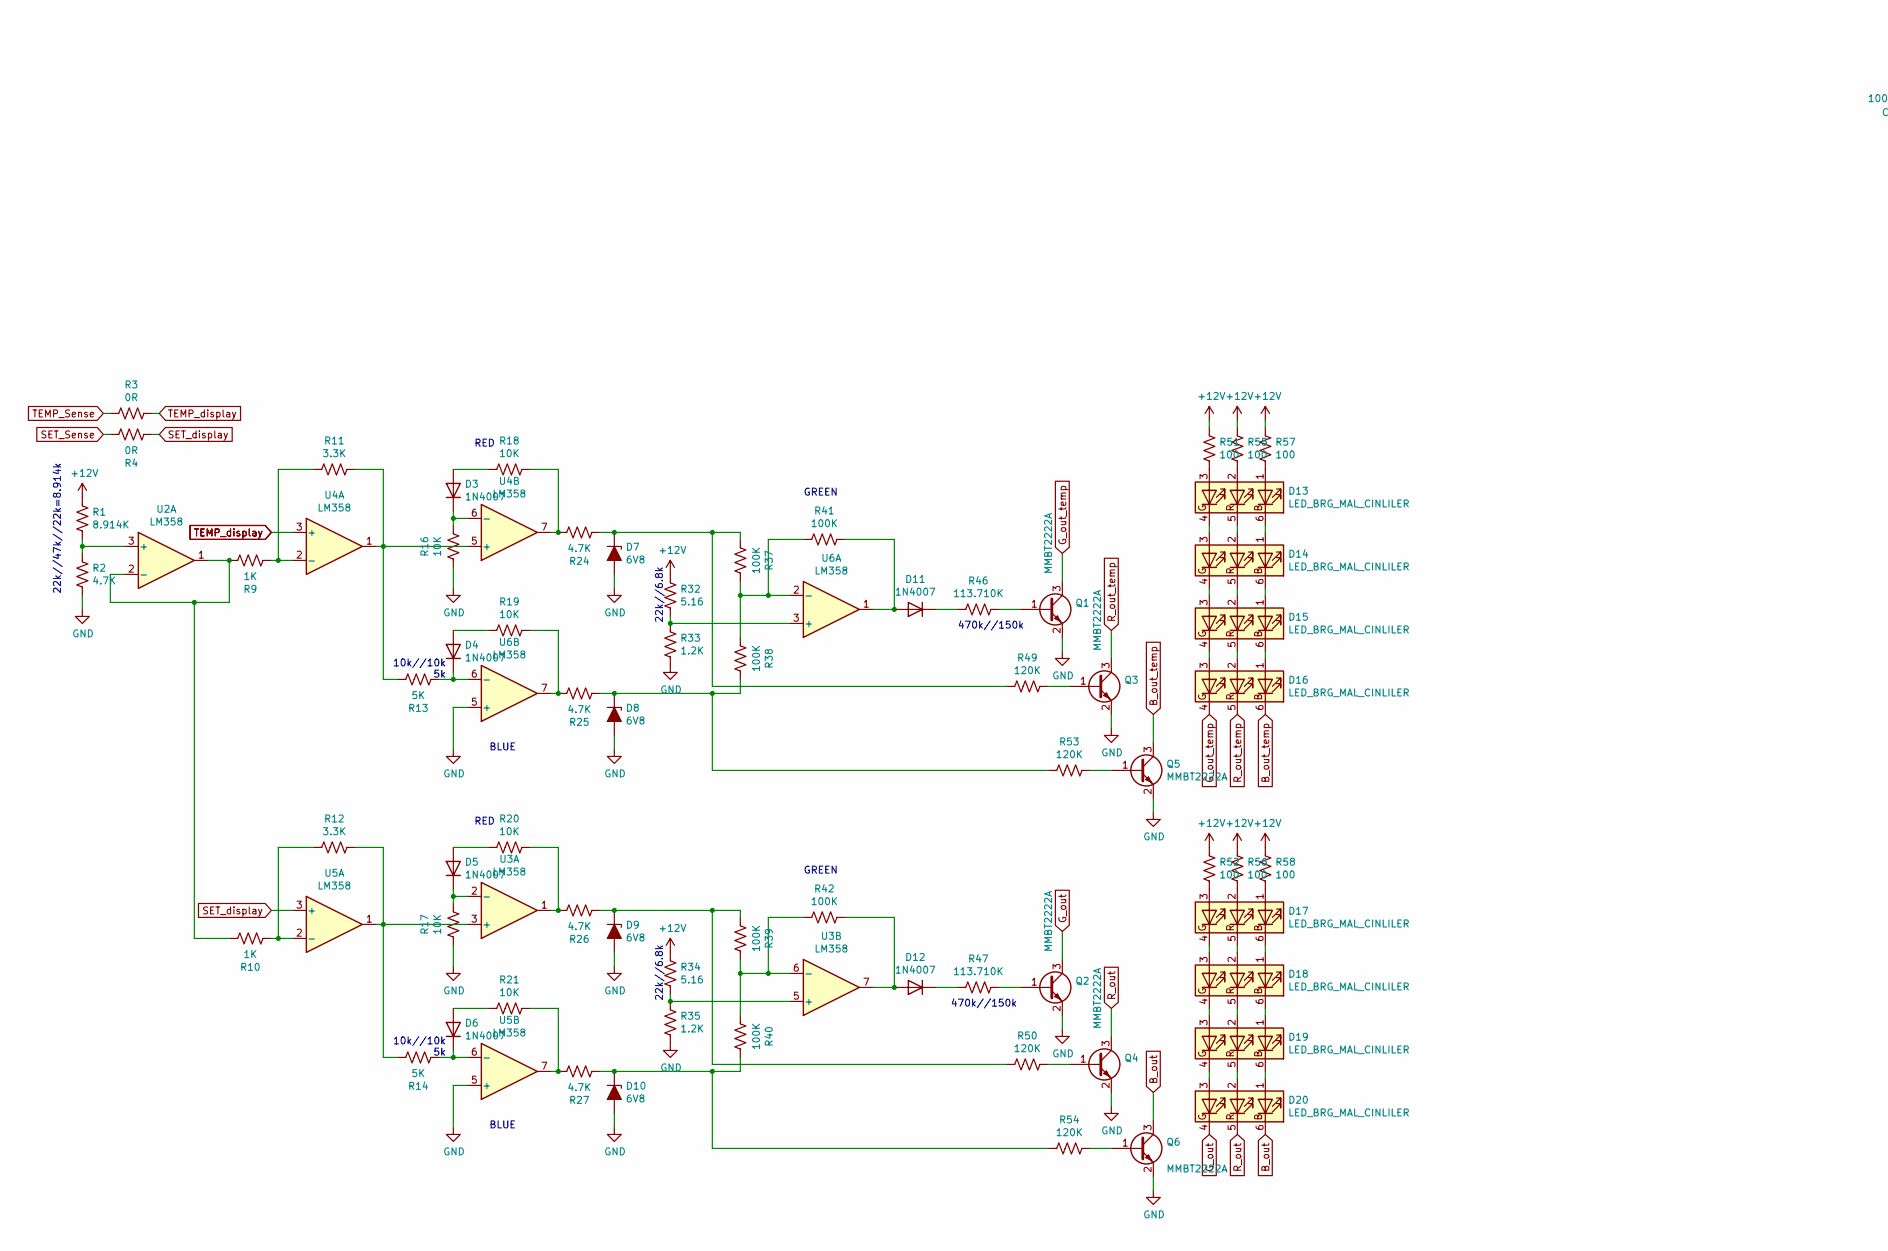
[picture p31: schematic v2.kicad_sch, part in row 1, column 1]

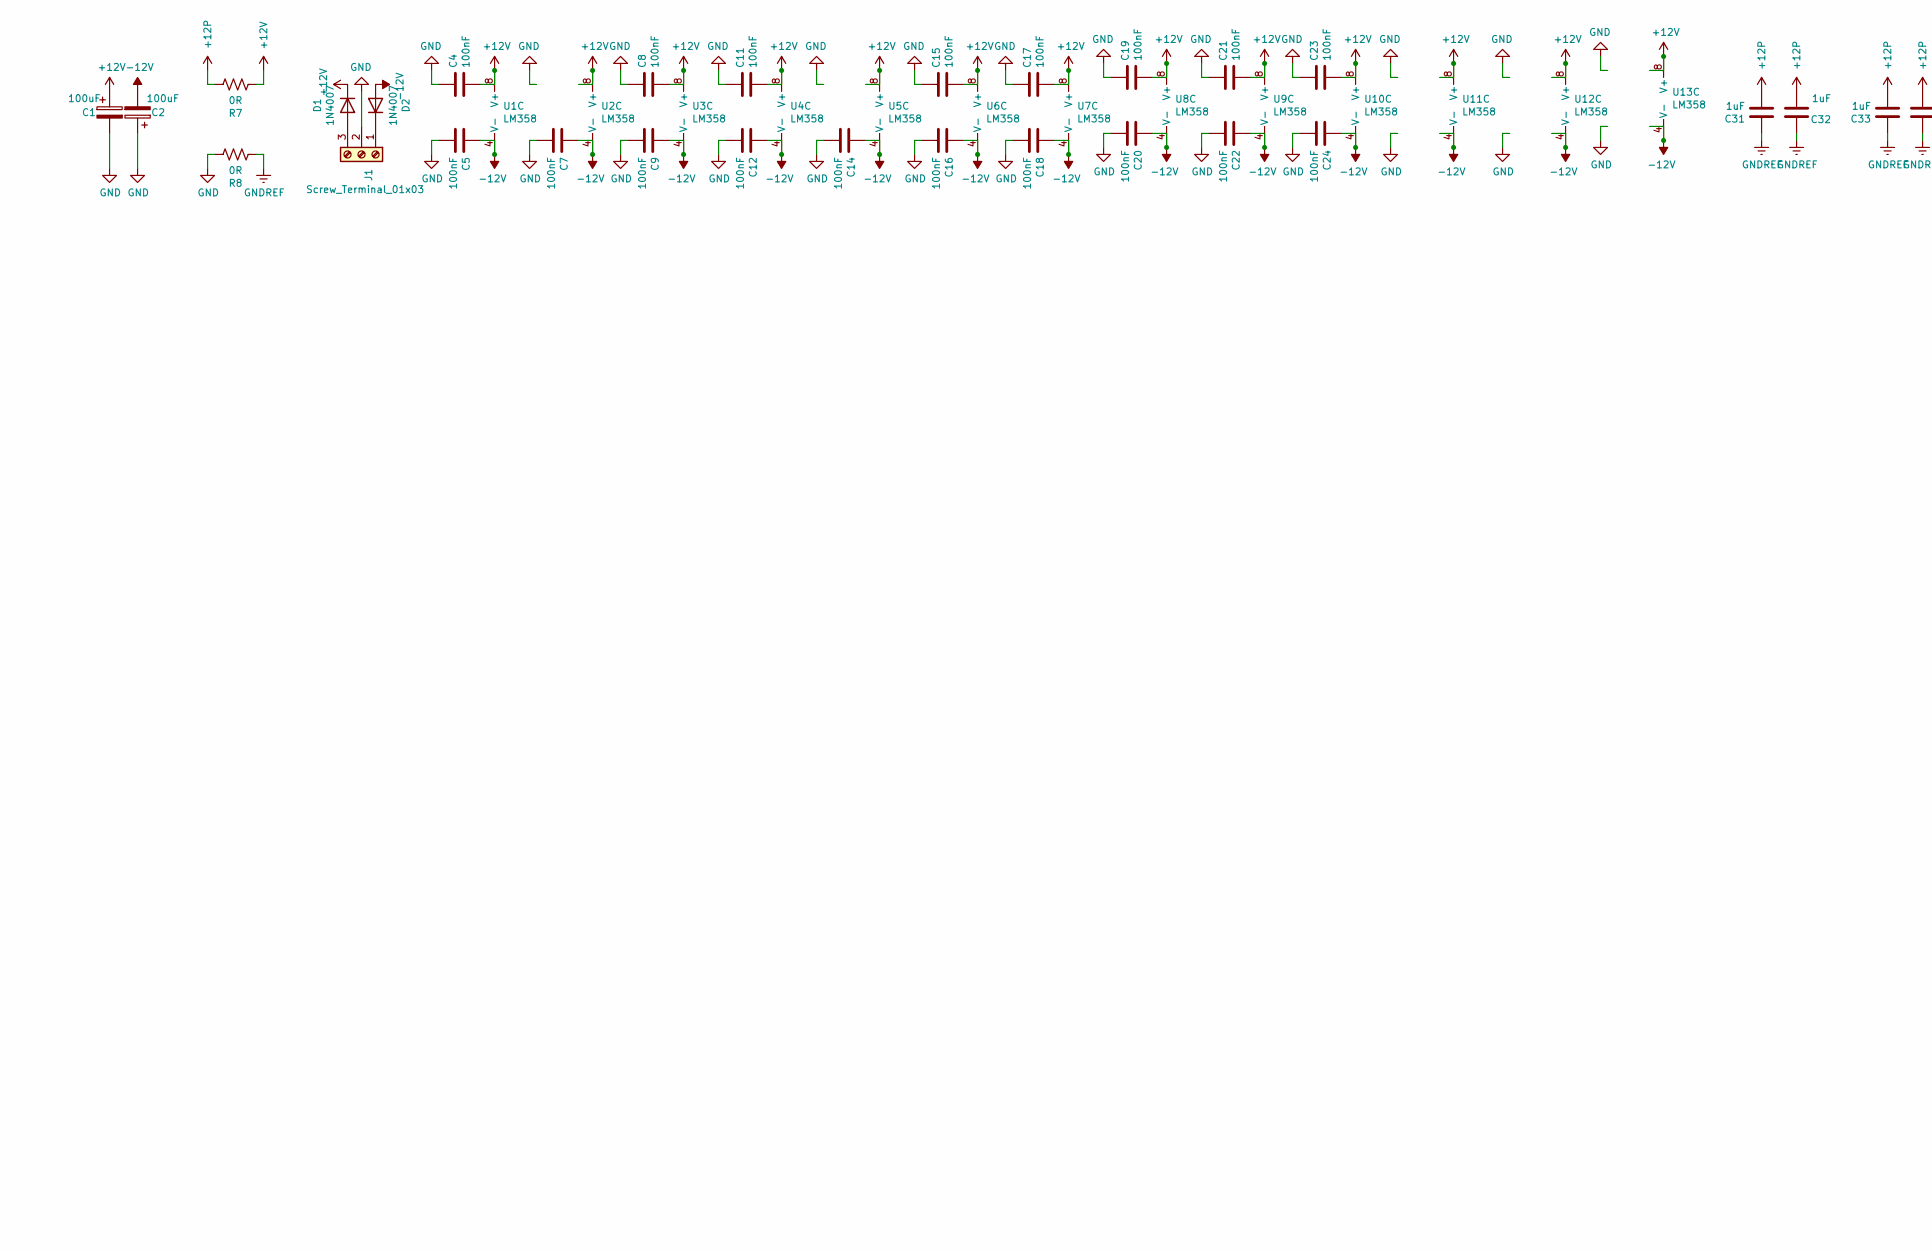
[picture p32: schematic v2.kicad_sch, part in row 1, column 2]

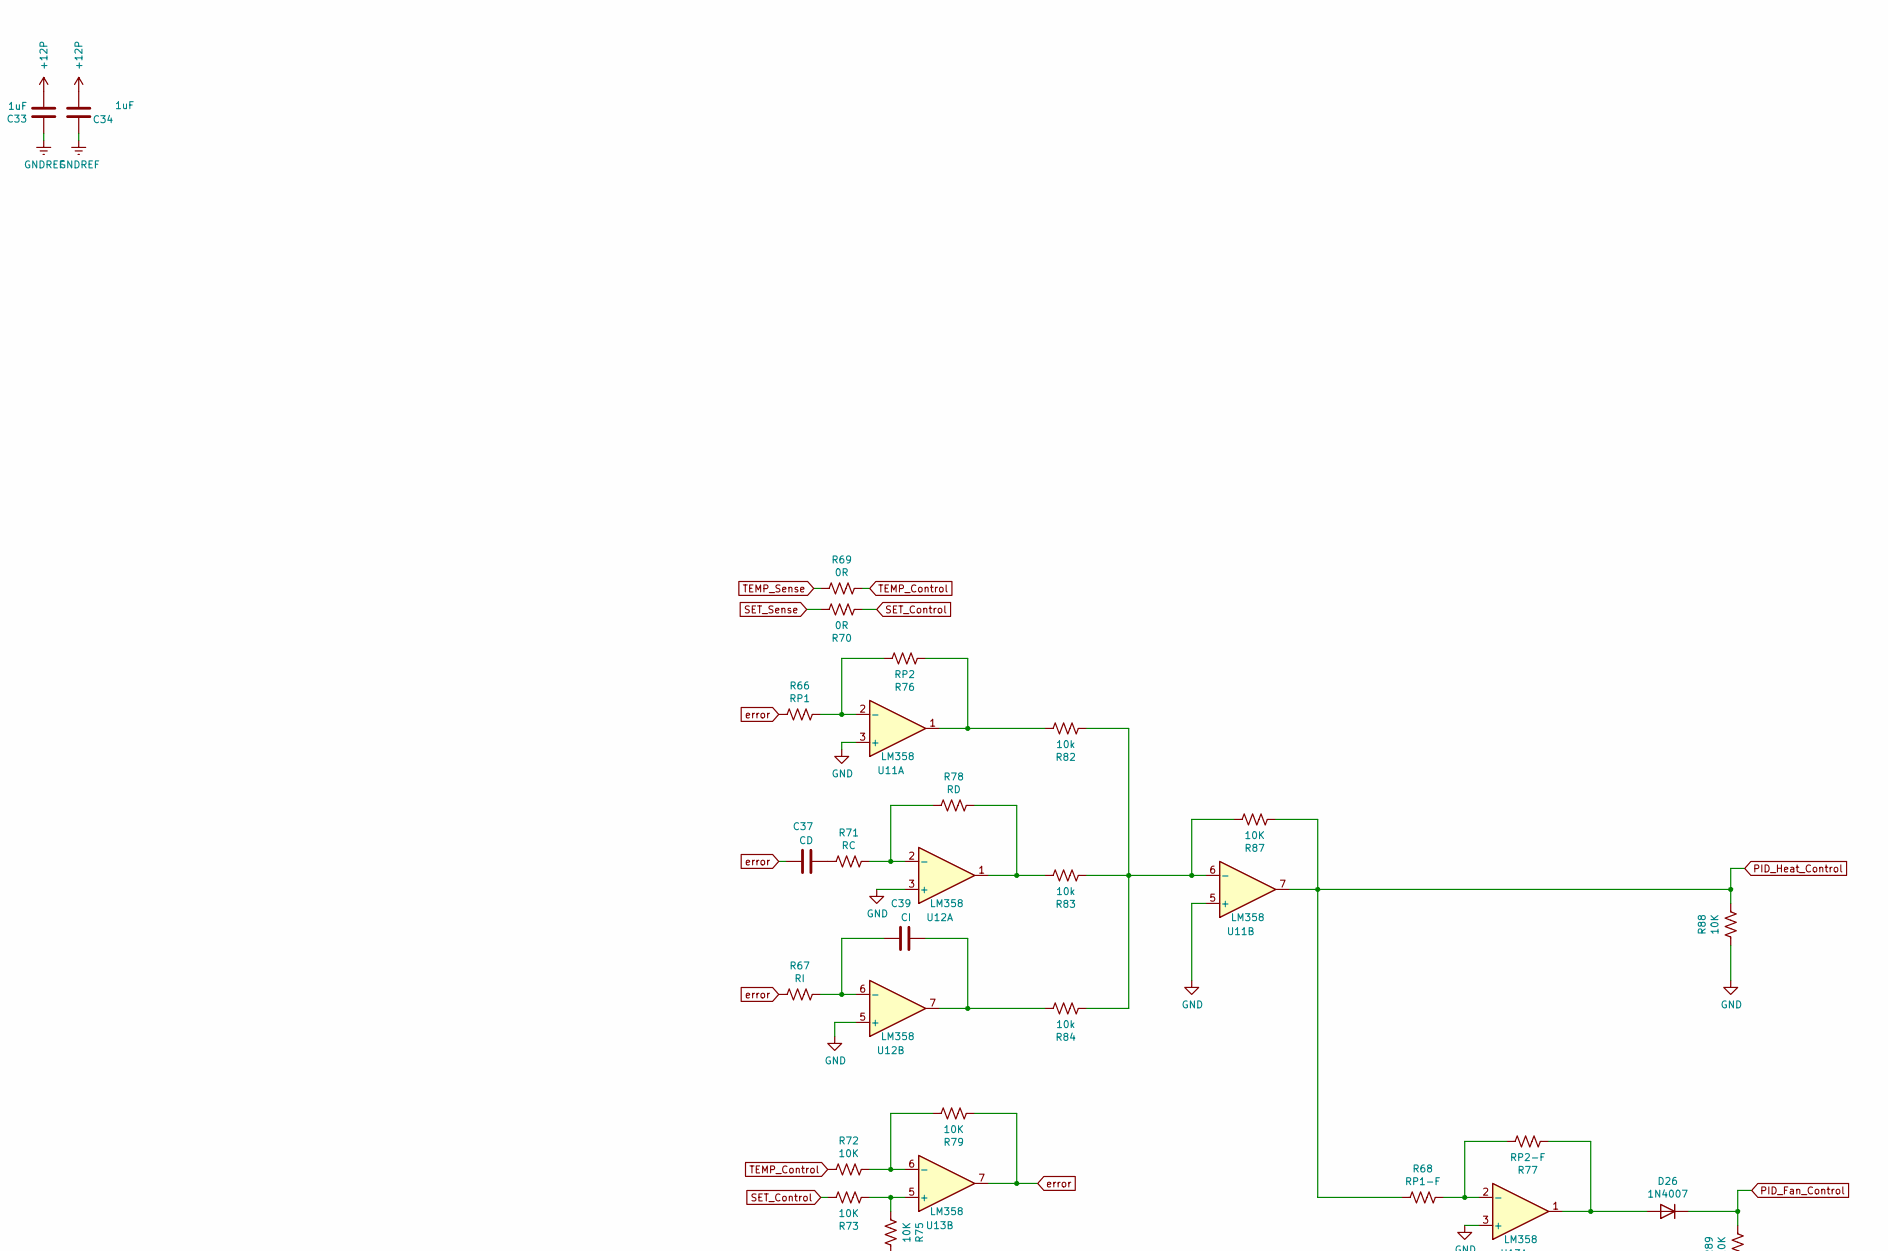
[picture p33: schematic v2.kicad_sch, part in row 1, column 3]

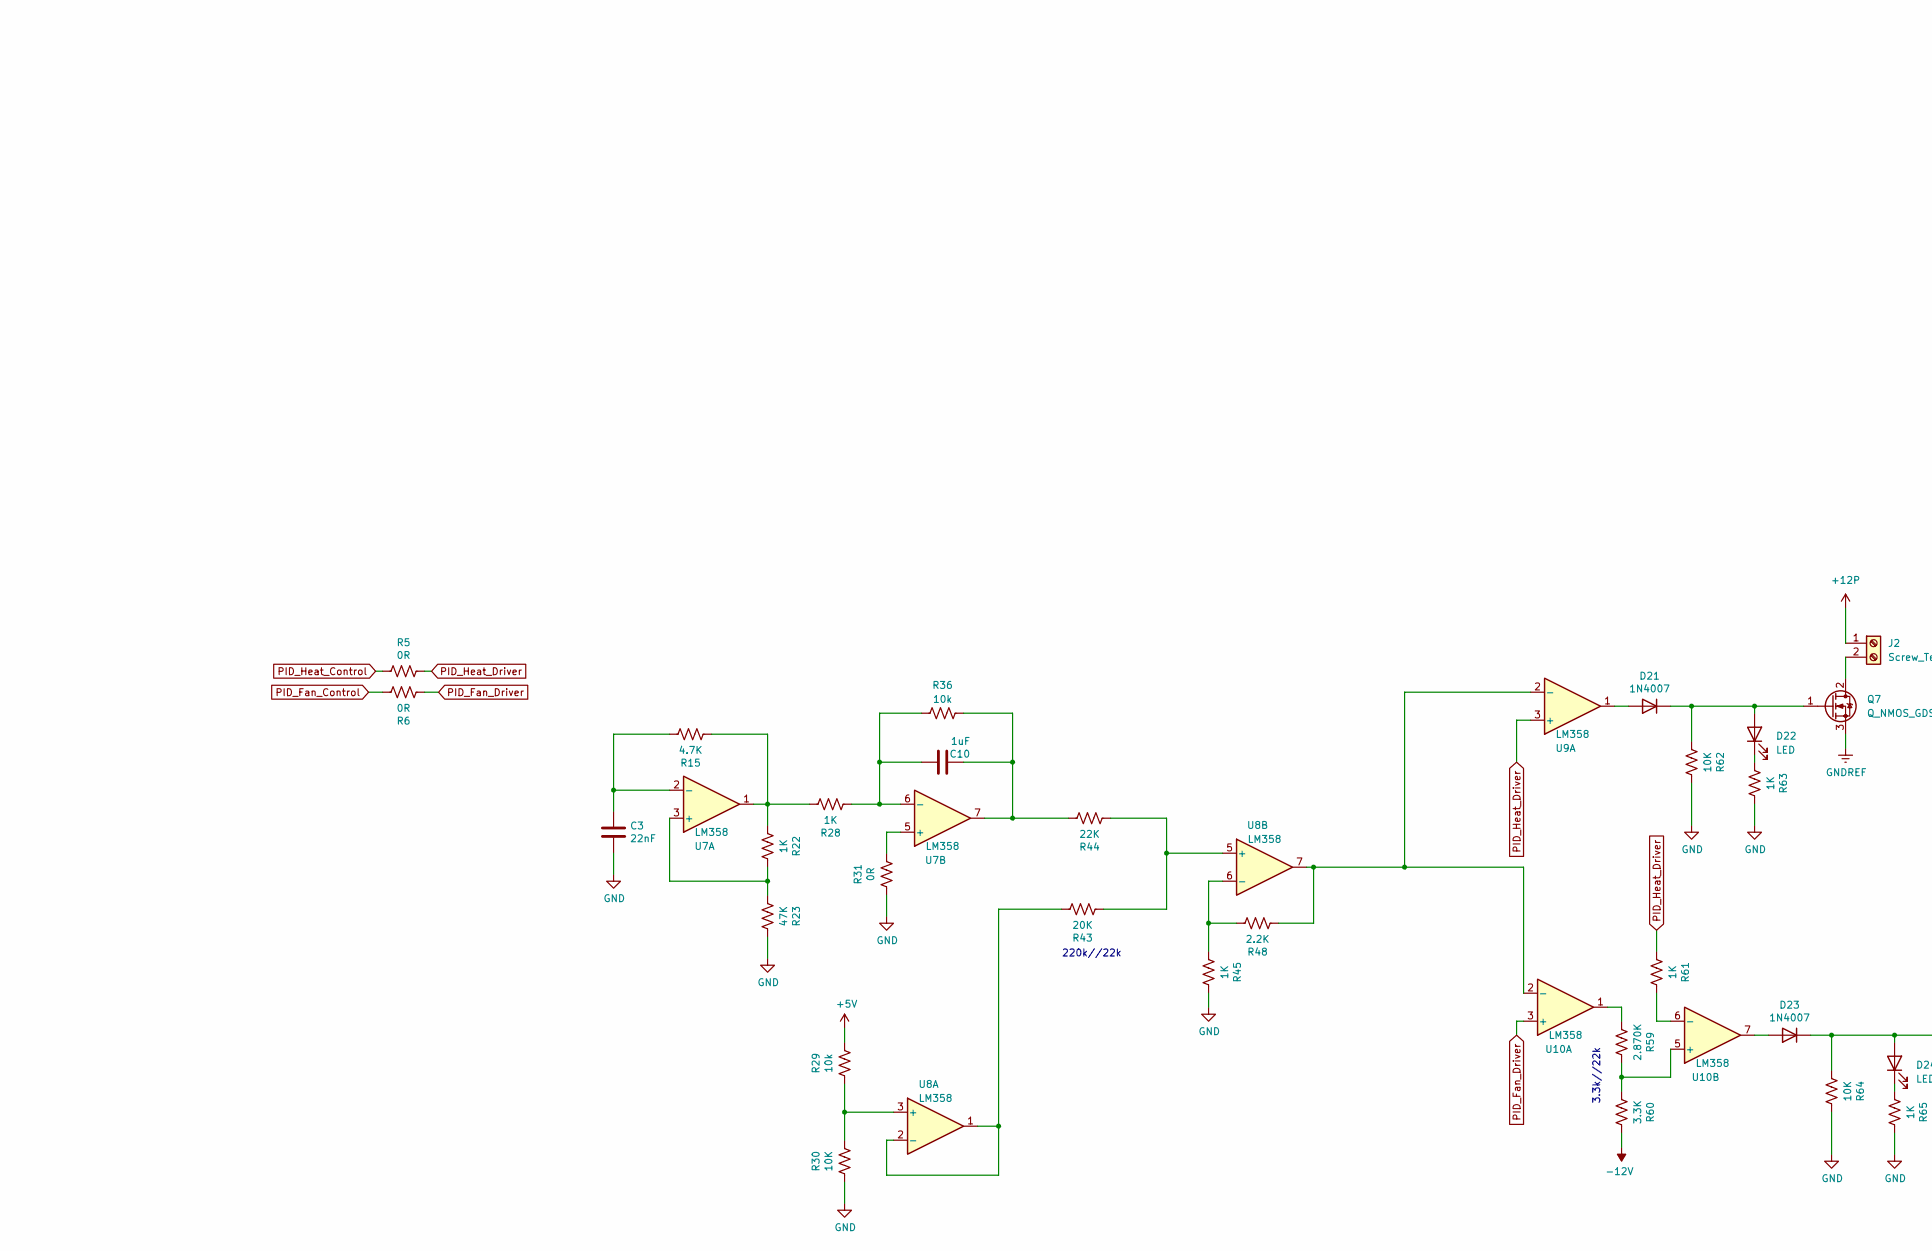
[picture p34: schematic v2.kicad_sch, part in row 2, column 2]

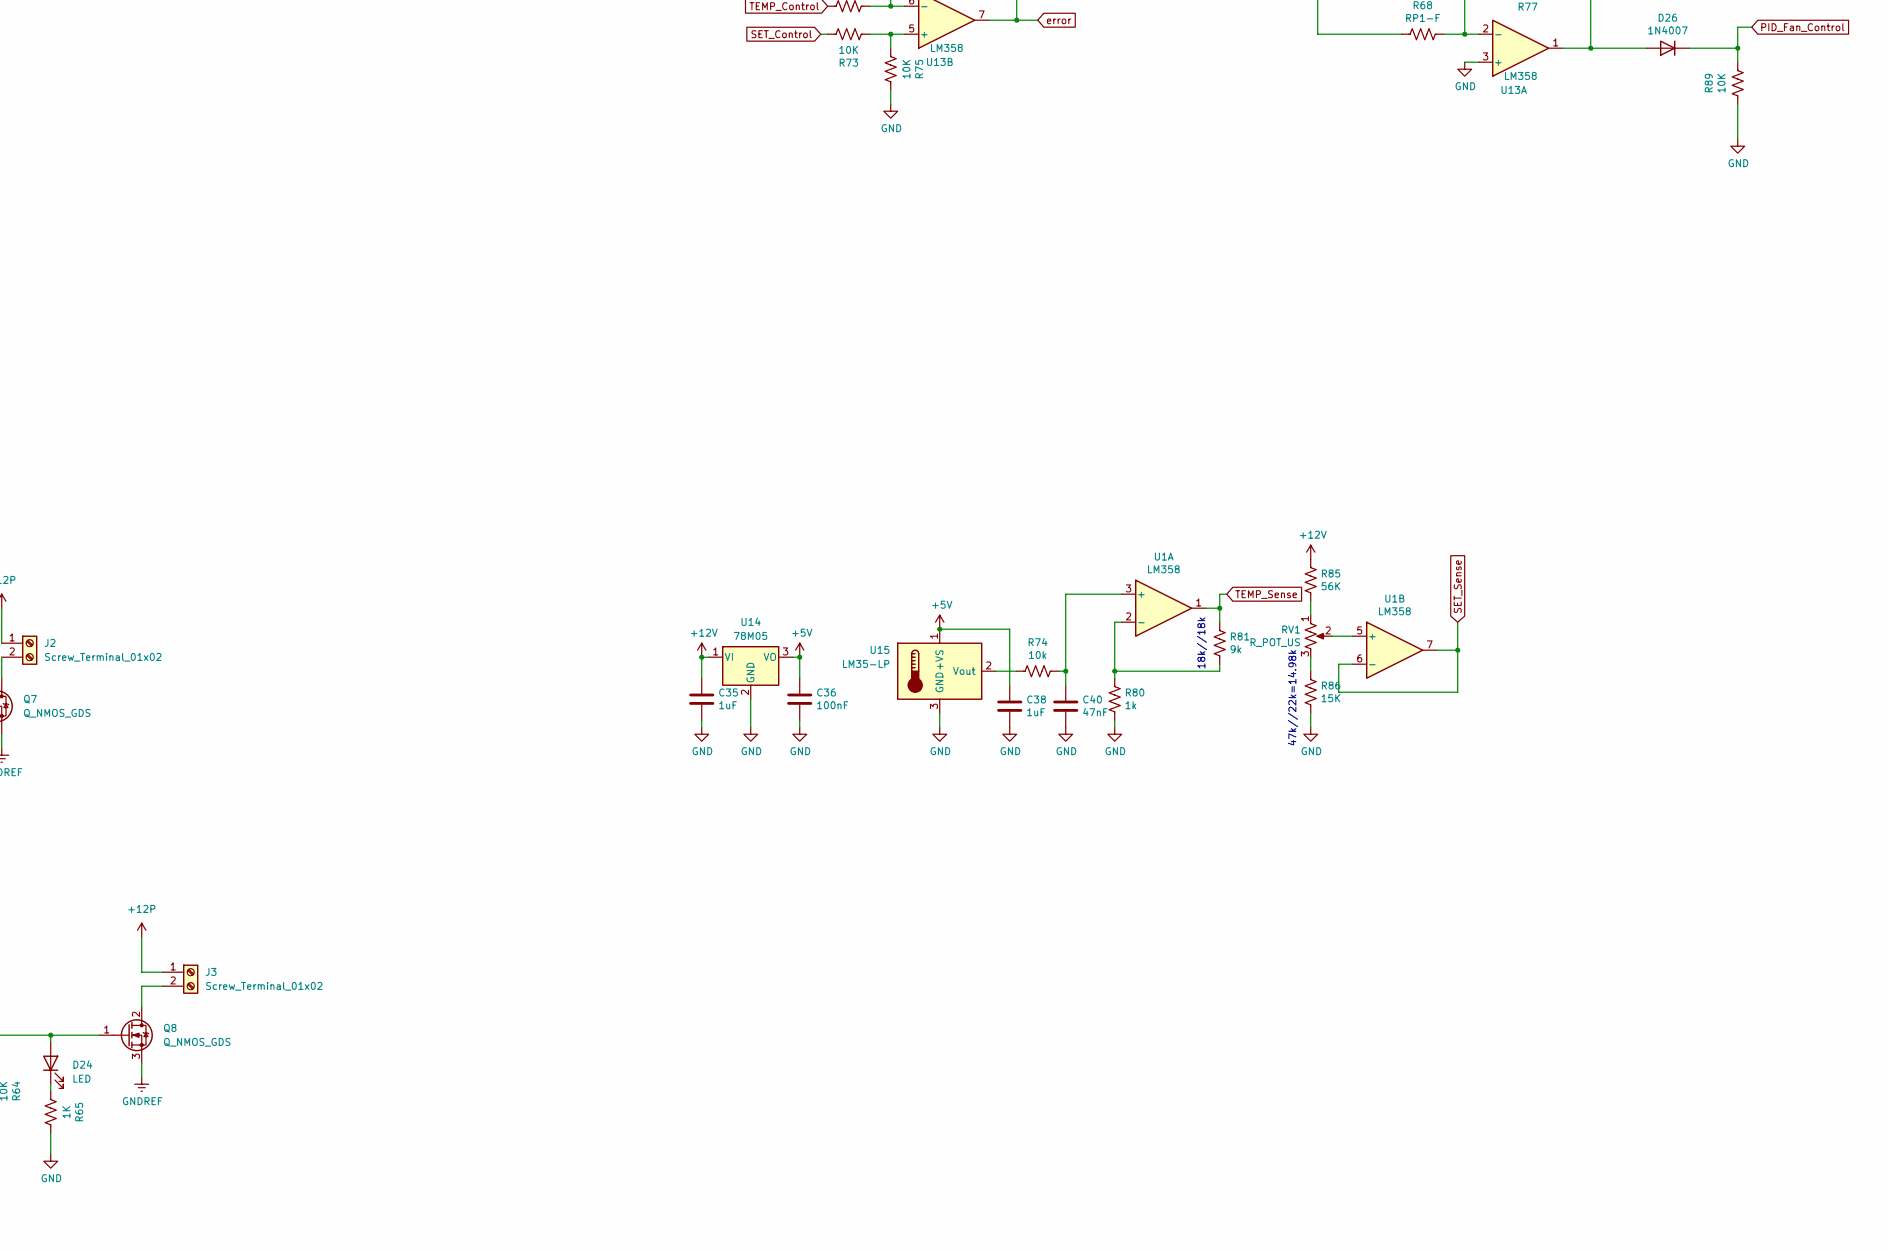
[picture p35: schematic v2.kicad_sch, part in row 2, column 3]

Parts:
C1, C2: 100uF; CP_Elec_6.3x5.7
C3: 22nF; R_1206_3216Metric_Pad1.30x1.75mm_HandSolder
C4, C5, C7, C8, C9, C11, C12, C14, C15, C16, C17, C18, C19, C20, C21, C22, C23, C24, C36: 100nF; R_1206_3216Metric_Pad1.30x1.75mm_HandSolder
C10, C31, C32, C33, C34, C35, C38: 1uF; R_1206_3216Metric_Pad1.30x1.75mm_HandSolder
C37: CD; R_1206_3216Metric_Pad1.30x1.75mm_HandSolder
C39: CI; R_1206_3216Metric_Pad1.30x1.75mm_HandSolder
C40: 47nF; R_0805_2012Metric_Pad1.20x1.40mm_HandSolder
D1, D2, D3, D4, D5, D6, D11, D12, D21, D23, D26: 1N4007; D_SMA_Handsoldering
D7, D8, D9, D10: 6V8; D_A-405_P5.08mm_Vertical_KathodeUp
D13, D14, D15, D16, D17, D18, D19, D20: LED_BRG_MAL_CINLILER; LED_RGB_5050-6
D22, D24: LED; R_1206_3216Metric_Pad1.30x1.75mm_HandSolder
J1: Screw_Terminal_01x03; DEGSONx3x3.81mm
J2, J3: Screw_Terminal_01x02; R_Axial_DIN0204_L3.6mm_D1.6mm_P1.90mm_Vertical
Q1, Q2, Q3, Q4, Q5, Q6: MMBT2222A
Q7, Q8: Q_NMOS_GDS; TO-252-2
R1: 8.914K; R_1206_3216Metric_Pad1.30x1.75mm_HandSolder
R2, R15, R24, R25, R26, R27: 4.7K; R_1206_3216Metric_Pad1.30x1.75mm_HandSolder
R3, R4, R5, R6, R7, R8, R31, R69, R70: 0R; R_1206_3216Metric_Pad1.30x1.75mm_HandSolder
R9, R10, R22, R28, R45, R61, R63, R65: 1K; R_1206_3216Metric_Pad1.30x1.75mm_HandSolder
R11, R12, R60: 3.3K; R_1206_3216Metric_Pad1.30x1.75mm_HandSolder
R13, R14: 5K; R_1206_3216Metric_Pad1.30x1.75mm_HandSolder
R16, R17, R18, R19, R20, R21, R30, R62, R64, R72, R73, R75, R79, R87, R88, R89: 10K; R_1206_3216Metric_Pad1.30x1.75mm_HandSolder
R23: 47K; R_1206_3216Metric_Pad1.30x1.75mm_HandSolder
R29, R36, R74, R82, R83, R84: 10k; R_1206_3216Metric_Pad1.30x1.75mm_HandSolder
R32, R34: 5.16; R_1206_3216Metric_Pad1.30x1.75mm_HandSolder
R33, R35: 1.2K; R_1206_3216Metric_Pad1.30x1.75mm_HandSolder
R37, R38, R39, R40, R41, R42: 100K; R_1206_3216Metric_Pad1.30x1.75mm_HandSolder
R43: 20K; R_1206_3216Metric_Pad1.30x1.75mm_HandSolder
R44: 22K; R_1206_3216Metric_Pad1.30x1.75mm_HandSolder
R46, R47: 113.710K; R_1206_3216Metric_Pad1.30x1.75mm_HandSolder
R48: 2.2K; R_1206_3216Metric_Pad1.30x1.75mm_HandSolder
R49, R50, R53, R54: 120K; R_1206_3216Metric_Pad1.30x1.75mm_HandSolder
R51, R52, R55, R56, R57, R58: 100; R_1206_3216Metric_Pad1.30x1.75mm_HandSolder
R59: 2.870K; R_1206_3216Metric_Pad1.30x1.75mm_HandSolder
R66: RP1; R_1206_3216Metric_Pad1.30x1.75mm_HandSolder
R67: RI; R_1206_3216Metric_Pad1.30x1.75mm_HandSolder
R68: RP1-F; R_1206_3216Metric_Pad1.30x1.75mm_HandSolder
R71: RC; R_1206_3216Metric_Pad1.30x1.75mm_HandSolder
R76: RP2; R_1206_3216Metric_Pad1.30x1.75mm_HandSolder
R77: RP2-F; R_1206_3216Metric_Pad1.30x1.75mm_HandSolder
R78: RD; R_1206_3216Metric_Pad1.30x1.75mm_HandSolder
R80: 1k; R_1206_3216Metric_Pad1.30x1.75mm_HandSolder
R81: 9k; R_1206_3216Metric_Pad1.30x1.75mm_HandSolder
R85: 56K; R_1206_3216Metric_Pad1.30x1.75mm_HandSolder
R86: 15K; R_1206_3216Metric_Pad1.30x1.75mm_HandSolder
RV1: R_POT_US; 20kpot
U1, U2, U3, U4, U5, U6, U7, U8, U9, U10, U11, U12, U13: LM358; SOIC-8_3.9x4.9mm_P1.27mm
U14: 78M05; TO-252-2
U15: LM35-LP; TO-92

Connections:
+5V: C36.1, C38.1, R29.2, U14.3 (VO), U15.1 (+VS); also elsewhere on the board
+12P: C31.2, C32.2, C33.2, C34.2, J2.1, J3.1, R7.2
+12V: C1.1, C4.2, C8.2, C11.2, C15.2, C17.2, C19.2, C21.2, C23.2, C35.1, D1.1 (K), R1.2, R7.1, R32.2, R34.2, R51.1, R52.1, R55.1, R56.1, R57.1, R58.1, R85.2, U1.8 (V+), U2.8 (V+), U3.8 (V+), U4.8 (V+), U5.8 (V+), U6.8 (V+), U7.8 (V+), U8.8 (V+), U9.8 (V+), U10.8 (V+), U11.8 (V+), U12.8 (V+), U13.8 (V+), U14.1 (VI)
-12V: C2.2, C5.1, C7.1, C9.1, C12.1, C14.1, C16.1, C18.1, C20.1, C22.1, C24.1, D2.2 (A), R60.2, U1.4 (V-), U2.4 (V-), U3.4 (V-), U4.4 (V-), U5.4 (V-), U6.4 (V-), U7.4 (V-), U8.4 (V-), U9.4 (V-), U10.4 (V-), U11.4 (V-), U12.4 (V-), U13.4 (V-)
B_out: D20.6 (RA), Q6.3 (C)
B_out_temp: D16.6 (RA), Q5.3 (C)
G_out: D20.4 (BA), Q2.3 (C)
G_out_temp: D16.4 (BA), Q1.3 (C)
unnamed: C3.1, R15.2, U7.2 (-)
unnamed: C10.1, R28.1, R36.2, U7.6 (-)
unnamed: C10.2, R36.1, R44.2, U7.7
unnamed: C37.2, R71.1
unnamed: C39.1, R67.2, U12.6 (-)
unnamed: C39.2, R84.2, U12.7
unnamed: C40.1, R74.1, U1.3 (+)
unnamed: D1.2 (A), J1.3
unnamed: D2.1 (K), J1.1
unnamed: D3.1 (K), R16.2, U4.6 (-)
unnamed: D3.2 (A), R18.1
unnamed: D4.1 (K), R13.1, U6.6 (-)
unnamed: D4.2 (A), R19.1
unnamed: D5.1 (K), R17.2, U3.2 (-)
unnamed: D5.2 (A), R20.1
unnamed: D6.1 (K), R14.1, U5.6 (-)
unnamed: D6.2 (A), R21.1
unnamed: D7.1 (K), R24.1, R37.1, R49.1
unnamed: D8.1 (K), R25.1, R38.2, R53.1
unnamed: D9.1 (K), R26.1, R39.1, R50.1
unnamed: D10.1 (K), R27.1, R40.2, R54.1
unnamed: D11.1 (K), R46.1
unnamed: D11.2 (A), R41.2, U6.1
unnamed: D12.1 (K), R47.1
unnamed: D12.2 (A), R42.2, U3.7
unnamed: D13.1 (RK), R57.2
unnamed: D13.2 (GK), R55.2
unnamed: D13.3 (BK), R51.2
unnamed: D13.4 (BA), D14.3 (BK)
unnamed: D13.5 (GA), D14.2 (GK)
unnamed: D13.6 (RA), D14.1 (RK)
unnamed: D14.4 (BA), D15.3 (BK)
unnamed: D14.5 (GA), D15.2 (GK)
unnamed: D14.6 (RA), D15.1 (RK)
unnamed: D15.4 (BA), D16.3 (BK)
unnamed: D15.5 (GA), D16.2 (GK)
unnamed: D15.6 (RA), D16.1 (RK)
unnamed: D17.1 (RK), R58.2
unnamed: D17.2 (GK), R56.2
unnamed: D17.3 (BK), R52.2
unnamed: D17.4 (BA), D18.3 (BK)
unnamed: D17.5 (GA), D18.2 (GK)
unnamed: D17.6 (RA), D18.1 (RK)
unnamed: D18.4 (BA), D19.3 (BK)
unnamed: D18.5 (GA), D19.2 (GK)
unnamed: D18.6 (RA), D19.1 (RK)
unnamed: D19.4 (BA), D20.3 (BK)
unnamed: D19.5 (GA), D20.2 (GK)
unnamed: D19.6 (RA), D20.1 (RK)
unnamed: D21.1 (K), D22.2 (A), Q7.1 (G), R62.1
unnamed: D21.2 (A), U9.1
unnamed: D22.1 (K), R63.1
unnamed: D23.1 (K), D24.2 (A), Q8.1 (G), R64.1
unnamed: D23.2 (A), U10.7
unnamed: D24.1 (K), R65.1
unnamed: D26.2 (A), R77.1, U13.1
unnamed: J2.2, Q7.2 (D)
unnamed: J3.2, Q8.2 (D)
unnamed: Q1.1 (B), R46.2
unnamed: Q2.1 (B), R47.2
unnamed: Q3.1 (B), R49.2
unnamed: Q4.1 (B), R50.2
unnamed: Q5.1 (B), R53.2
unnamed: Q6.1 (B), R54.2
unnamed: R1.1, R2.2, U2.3 (+)
unnamed: R10.1, R12.1, U5.2 (-)
unnamed: R9.2, R10.2, U2.1, U2.2 (-)
unnamed: R9.1, R11.1, U4.2 (-)
unnamed: R11.2, R13.2, U4.1, U4.5 (+)
unnamed: R12.2, R14.2, U3.3 (+), U5.1
unnamed: R15.1, R22.1, R28.2, U7.1
unnamed: R18.2, R24.2, U4.7
unnamed: R19.2, R25.2, U6.7
unnamed: R20.2, R26.2, U3.1
unnamed: R21.2, R27.2, U5.7
unnamed: R22.2, R23.1, U7.3 (+)
unnamed: R29.1, R30.2, U8.3 (+)
unnamed: R31.2, U7.5 (+)
unnamed: R32.1, R33.2, U6.3 (+)
unnamed: R34.1, R35.2, U3.5 (+)
unnamed: R37.2, R38.1, R41.1, U6.2 (-)
unnamed: R39.2, R40.1, R42.1, U3.6 (-)
unnamed: R43.1, R44.1, U8.5 (+)
unnamed: R43.2, U8.1, U8.2 (-)
unnamed: R45.1, R48.2, U8.6 (-)
unnamed: R48.1, U8.7, U9.2 (-), U10.2 (-)
unnamed: R59.1, U10.1
unnamed: R59.2, R60.1, U10.5 (+)
unnamed: R61.2, U10.6 (-)
unnamed: R66.2, R76.2, U11.2 (-)
unnamed: R68.2, R77.2, U13.2 (-)
unnamed: R71.2, R78.1, U12.2 (-)
unnamed: R72.2, R79.2, U13.6 (-)
unnamed: R73.1, R75.1, U13.5 (+)
unnamed 102: R74.2, U15.2 (Vout); also elsewhere on the board
unnamed: R76.1, R82.2, U11.1
unnamed: R78.2, R83.2, U12.1
unnamed: R80.2, R81.1, U1.2 (-)
unnamed: R82.1, R83.1, R84.1, R87.2, U11.6 (-)
unnamed: R85.1, RV1.1
unnamed: R86.2, RV1.3
unnamed: RV1.2, U1.5 (+)
PID_Fan_Control: D26.1 (K), R6.2, R89.2
PID_Fan_Driver: R6.1, U10.3 (+)
PID_Heat_Driver: R5.2, R61.1, U9.3 (+)
R_out: D20.5 (GA), Q4.3 (C)
R_out_temp: D16.5 (GA), Q3.3 (C)
SET_Control: R70.1, R73.2
SET_Sense: R4.2, R70.2, U1.6 (-), U1.7
SET_display: R4.1, U5.3 (+)
TEMP_Control: R69.2, R72.1
TEMP_Sense: R3.1, R69.1, R81.2, U1.1
TEMP_display: R3.2, U4.3 (+)

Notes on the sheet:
220k//22k
GREEN
22k//47k//22k=8.914k
RED
10k//10k 5k
470k//150k
22k//6.8k
47k//22k=14.98k
3.3k//22k
BLUE
18k//18k

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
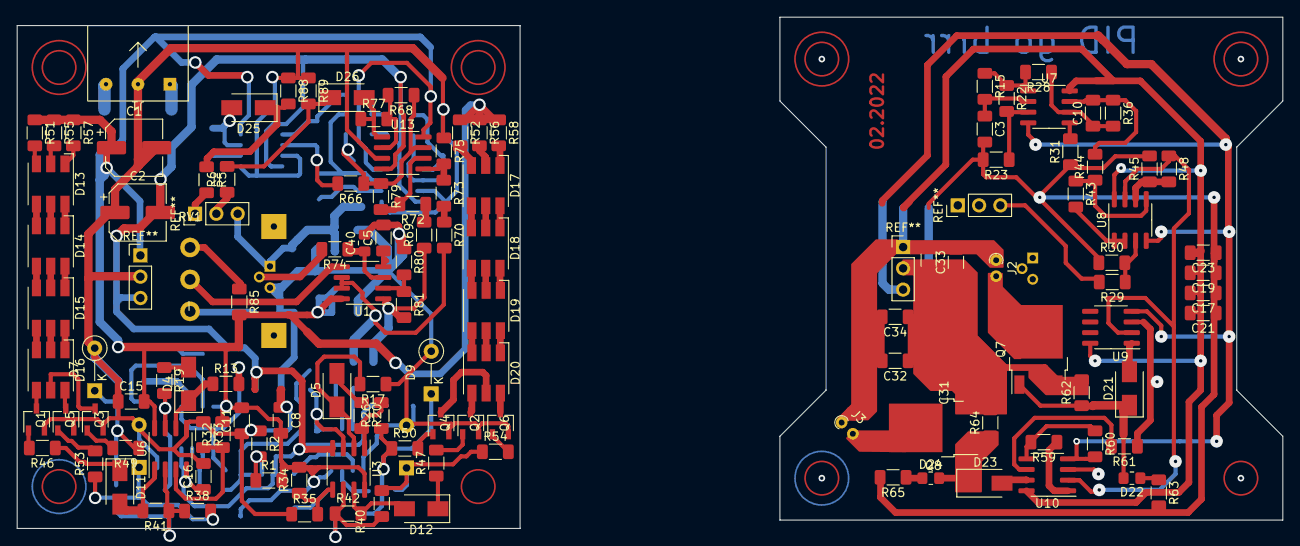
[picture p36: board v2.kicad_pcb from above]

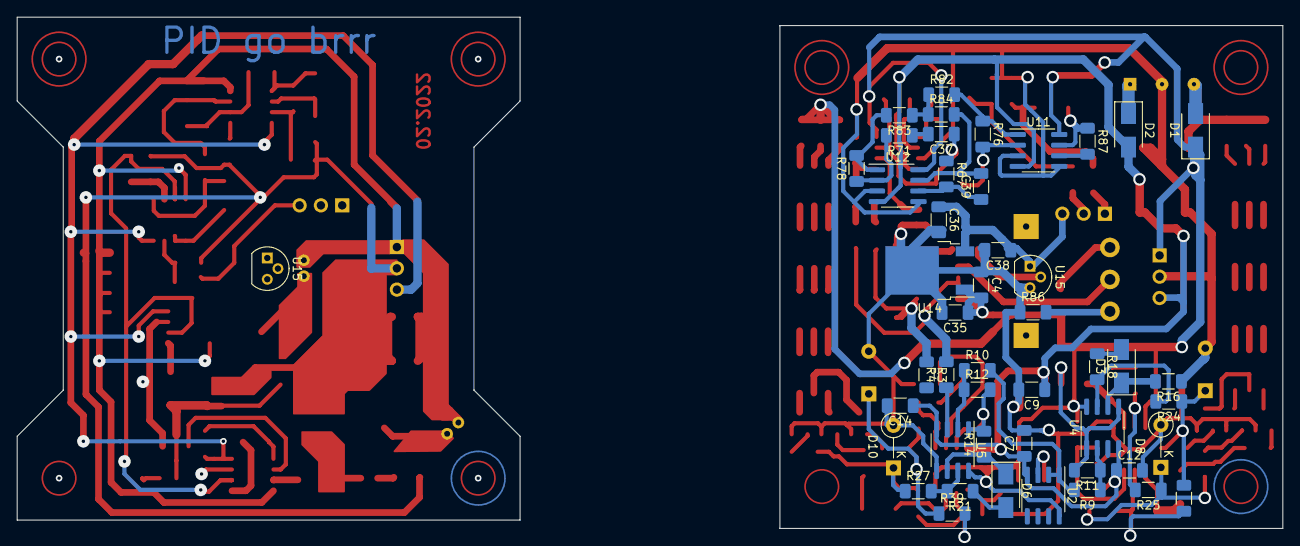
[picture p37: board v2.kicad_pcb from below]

Board: 4 copper layers, 151.0 x 61.0 mm, 169 parts (48 on the bottom side), 126 nets.

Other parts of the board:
D25: 1N4007; D_SMA
U15#2: LM35-LP; TO-92

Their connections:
+5V: U15#2.1 (+VS); also elsewhere on the board
unnamed 102: U15#2.2 (Vout); also elsewhere on the board

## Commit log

2022-01-16 first report phase has passed
    [Fan 60x60x25mm.stp, Package, SOIC-8, 3.9mm.STEP, TO-92.stp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]
2022-03-05 Add files via upload
    pcb exports from kicad
    [PCBs.step]
2022-03-05 Add files via upload
    pcb projects are added
    [v1.kicad_pcb, v1.kicad_sch, v1.sch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]
2022-03-05 Add files via upload
    pcb outputs in pdf format
2022-07-26 [Reallocation] organizing the folders
    [Fan 60x60x25mm.stp, PCBs.step, Package, SOIC-8, 3.9mm.STEP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]
